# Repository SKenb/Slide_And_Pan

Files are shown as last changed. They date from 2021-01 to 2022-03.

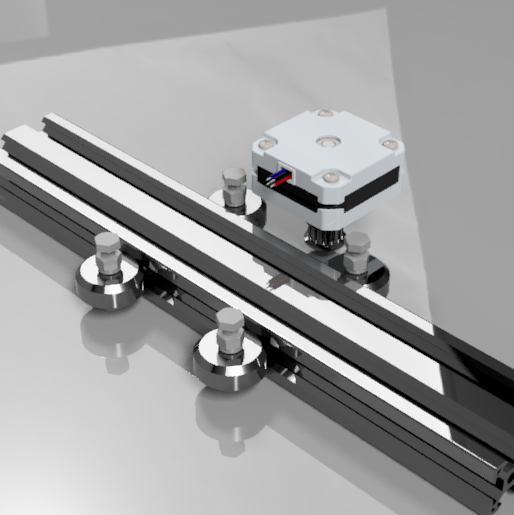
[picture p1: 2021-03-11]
Construction/Images/Slider_2 v50_SlideModule_FrontLeft.png

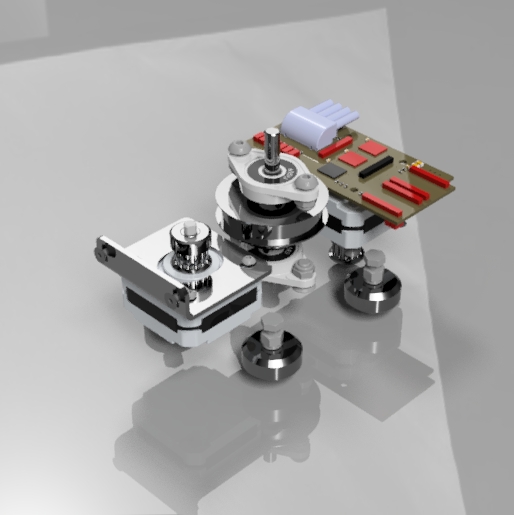
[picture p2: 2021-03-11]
Construction/Images/Slider_2 v50_N_5.png

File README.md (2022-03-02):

# Slide and Pan

## Overview 

    To give a timelapse that special touch, movement is essential. With this simple self-made and inexpensive slider, one can easily achieve that.

"Slide and Pan" stands for a small, compact, and "all in one" DIY slider.

### All in one

_Just place the Slider and start shooting._

The solution provides one small, solid metal box. (55 x 50 x 145 mm - TODO kg). So all required electronics and mechanics in it and no further motors, batteries, control devices are needed.

### Cheap

_Adjust the expenses to your budget._

One key argument for building an own Slider is the relatively small expenses compared to conventional Sliders. One might also think of requesting prepared or finished parts within a fair price ...

### DIY

_You are the boss_

The plans are no secret and easily be replicated by yourself. Just have a look at the public construction plans or come up with your own modified version.

### App

_Easy control_

Use the built-in rotary encoder or the App, to control the Slider. The App makes it very comfortable to set up movements and plan your shots.

## FEATURES

### Slide

Add linear movement to your Timelapse with the Slide-Feature.
Thereby, the Slider moves along a normed Alu-Profile, and thus any length you can think of is possible...

### Pan

Add some gorgeous rotation to your Timelapse
Keep the Milky Way in the center of the frame or focus another lovely spot during your shooting with the feature of (infinity) rotation of your camera ...

### TRACK

Use the Slider as Star-Tracker and realize detailed DeepSky exposures....

### Control

Select one of the predefined shots with the rotary-encoder or set up a detailed exposure/Timelapse with the inbuilt App...

### Compact

One of the most important factors is to have a small, compact and all in one gadget which fits in every backpack...

### Standalone

Everything included and thus no additional material is needed...

### Powerful

2 x 1500 mAh
Two powerful LiPo-batteries provide Slider with enough energy for several hours of shooting....

### Versatile

Nearly every position and movement one might think of is possible ...

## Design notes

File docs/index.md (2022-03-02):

# Slide and Pan

## Overview 

    To give a timelapse that special touch, movement is essential. With this simple self-made and inexpensive slider, one can easily achieve that.

"Slide and Pan" stands for a small, compact, and "all in one" DIY slider.

### All in one

_Just place the Slider and start shooting._

The solution provides one small, solid metal box. (55 x 50 x 145 mm - TODO kg). So all required electronics and mechanics in it and no further motors, batteries, control devices are needed.

### Cheap

_Adjust the expenses to your budget._

One key argument for building an own Slider is the relatively small expenses compared to conventional Sliders. One might also think of requesting prepared or finished parts within a fair price ...

### DIY

_You are the boss_

The plans are no secret and easily be replicated by yourself. Just have a look at the public construction plans or come up with your own modified version.

### App

_Easy control_

Use the built-in rotary encoder or the App, to control the Slider. The App makes it very comfortable to set up movements and plan your shots.

## FEATURES

### Slide

Add linear movement to your Timelapse with the Slide-Feature.
Thereby, the Slider moves along a normed Alu-Profile, and thus any length you can think of is possible...

### Pan

Add some gorgeous rotation to your Timelapse
Keep the Milky Way in the center of the frame or focus another lovely spot during your shooting with the feature of (infinity) rotation of your camera ...

### TRACK

Use the Slider as Star-Tracker and realize detailed DeepSky exposures....

### Control

Select one of the predefined shots with the rotary-encoder or set up a detailed exposure/Timelapse with the inbuilt App...

### Compact

One of the most important factors is to have a small, compact and all in one gadget which fits in every backpack...

### Standalone

Everything included and thus no additional material is needed...

### Powerful

2 x 1500 mAh
Two powerful LiPo-batteries provide Slider with enough energy for several hours of shooting....

### Versatile

Nearly every position and movement one might think of is possible ...

## Welcome to GitHub Pages

You can use the [editor on GitHub](https://github.com/SKenb/Slide_And_Pan/edit/master/docs/index.md) to maintain and preview the content for your website in Markdown files.

Whenever you commit to this repository, GitHub Pages will run [Jekyll](https://jekyllrb.com/) to rebuild the pages in your site, from the content in your Markdown files.

### Markdown

Markdown is a lightweight and easy-to-use syntax for styling your writing. It includes conventions for

```markdown
Syntax highlighted code block

# Header 1
## Header 2
### Header 3

- Bulleted
- List

1. Numbered
2. List

**Bold** and _Italic_ and `Code` text

[Link](url) and ![Image](src)
```

For more details see [Basic writing and formatting syntax](https://docs.github.com/en/github/writing-on-github/getting-started-with-writing-and-formatting-on-github/basic-writing-and-formatting-syntax).

### Jekyll Themes

Your Pages site will use the layout and styles from the Jekyll theme you have selected in your [repository settings](https://github.com/SKenb/Slide_And_Pan/settings/pages). The name of this theme is saved in the Jekyll `_config.yml` configuration file.

### Support or Contact

Having trouble with Pages? Check out our [documentation](https://docs.github.com/categories/github-pages-basics/) or [contact support](https://support.github.com/contact) and we’ll help you sort it out.

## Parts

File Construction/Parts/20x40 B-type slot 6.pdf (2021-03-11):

# Profile 20x40 B-Type slot 6

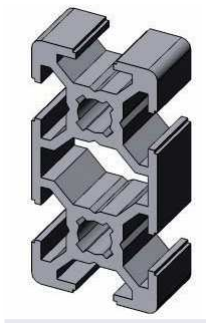
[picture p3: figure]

Profile 20x40 B-Type slot 6

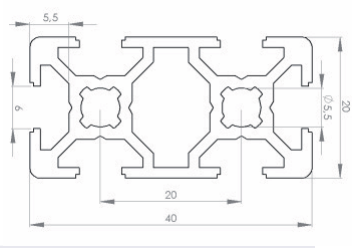
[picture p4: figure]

Slot | | 6 | mm
Mass | m | 0,80 | Kg/m
Moment of Inertia | Ix | 4,60 | cm⁴
| Iy | 1,20 | cm⁴
Section modulus | Wx | 2,50 | cm³
| Wy | 1,40 | cm³
Surface | A | 2,90 | cm²

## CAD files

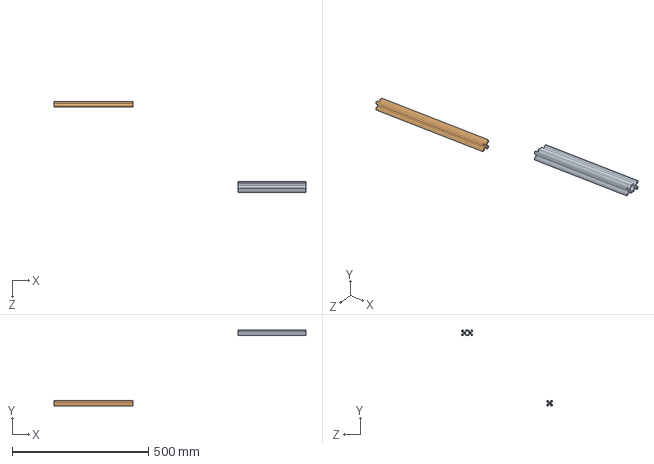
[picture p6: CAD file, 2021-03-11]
Construction/Parts/v-slot-profiles-20x20-20x40-1.snapshot.5/V - slot profiles (20x20 & 20x40).SLDASM
923.9 x 277.7 x 331.8 mm
v-20x40 alluminum profile
V-2020 alluminum profile

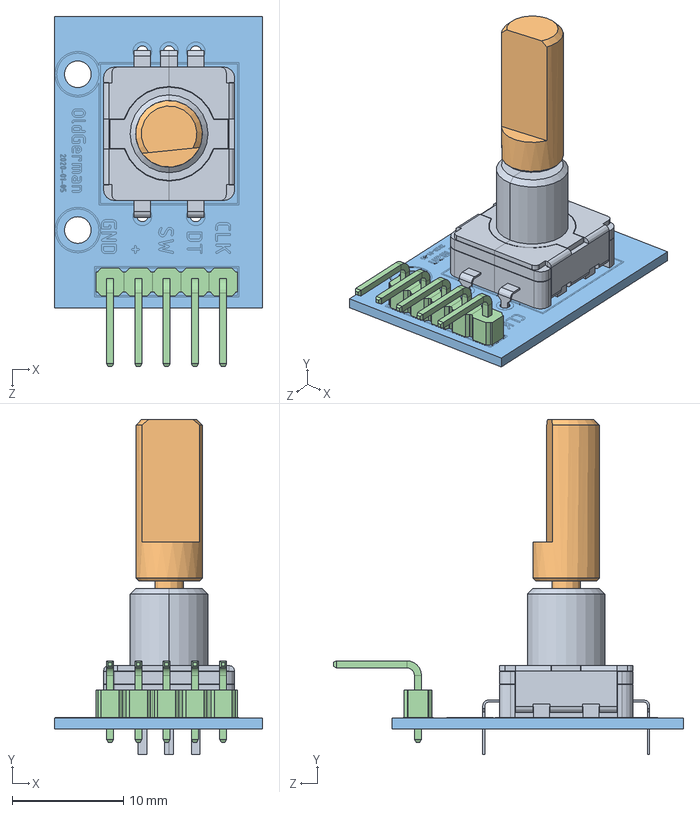
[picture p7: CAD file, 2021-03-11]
Construction/Parts/ky-040-rotary-encoder-1.snapshot.1/Rotary Encoder - ODG/sw2017 model/KY-040 Rotary Encoder.SLDASM
18.7 x 30.1 x 31.5 mm
Rotary Encoder
D-handle
pcb
2.54 5PIN 90

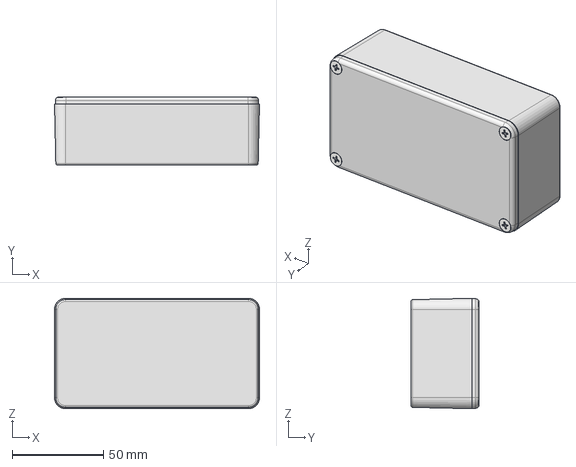
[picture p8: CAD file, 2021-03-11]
Construction/Parts/1590B2/1590B2.stp
112.4 x 37.5 x 60.5 mm
1590B2 BOX
1590B-BS LID

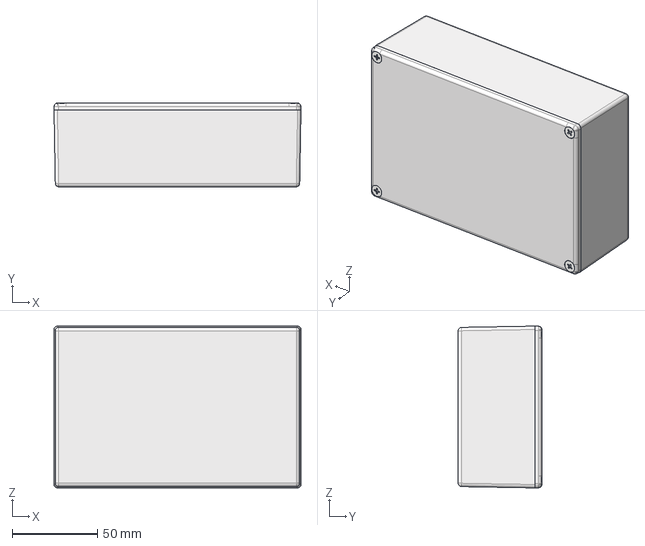
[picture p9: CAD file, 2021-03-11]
Construction/Parts/1590J/1590J.stp
145.0 x 49.1 x 95.0 mm

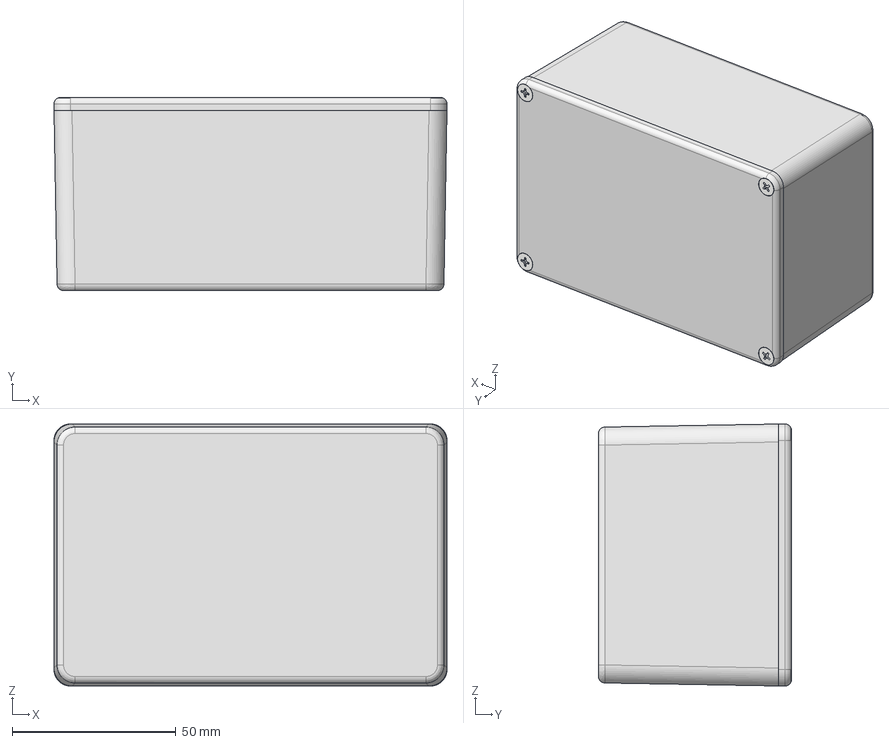
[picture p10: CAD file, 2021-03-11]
Construction/Parts/1590T/1590T.stp
120.0 x 59.0 x 80.0 mm

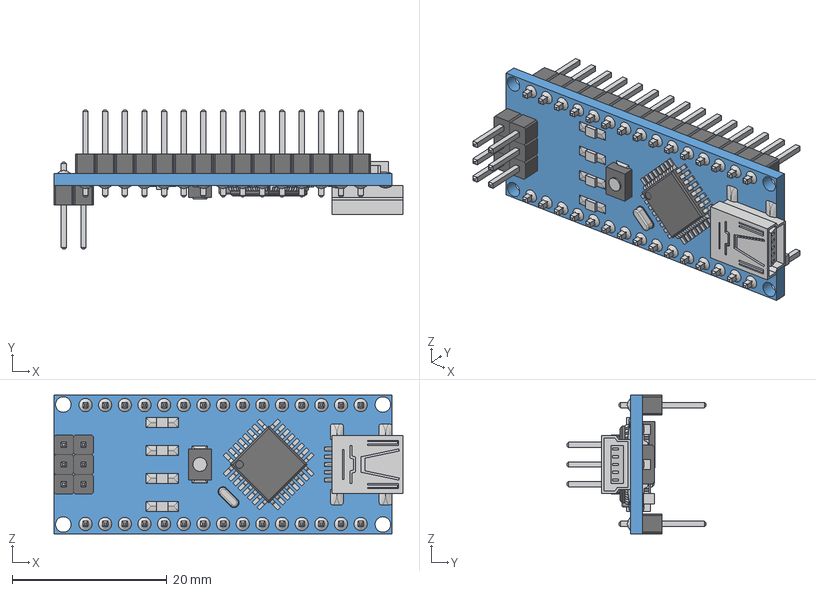
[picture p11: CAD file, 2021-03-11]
Construction/Parts/arduino-nano-v3-2.snapshot.6/Arduino Nano V3.step
45.1 x 18.0 x 17.9 mm
switch
Led x 3
Led (1)
Pin x 21
chip1
USB
Crystal
Pin (1) x 15
Res x 5
cap x 2
Chip
respack x 2
diode
vreg

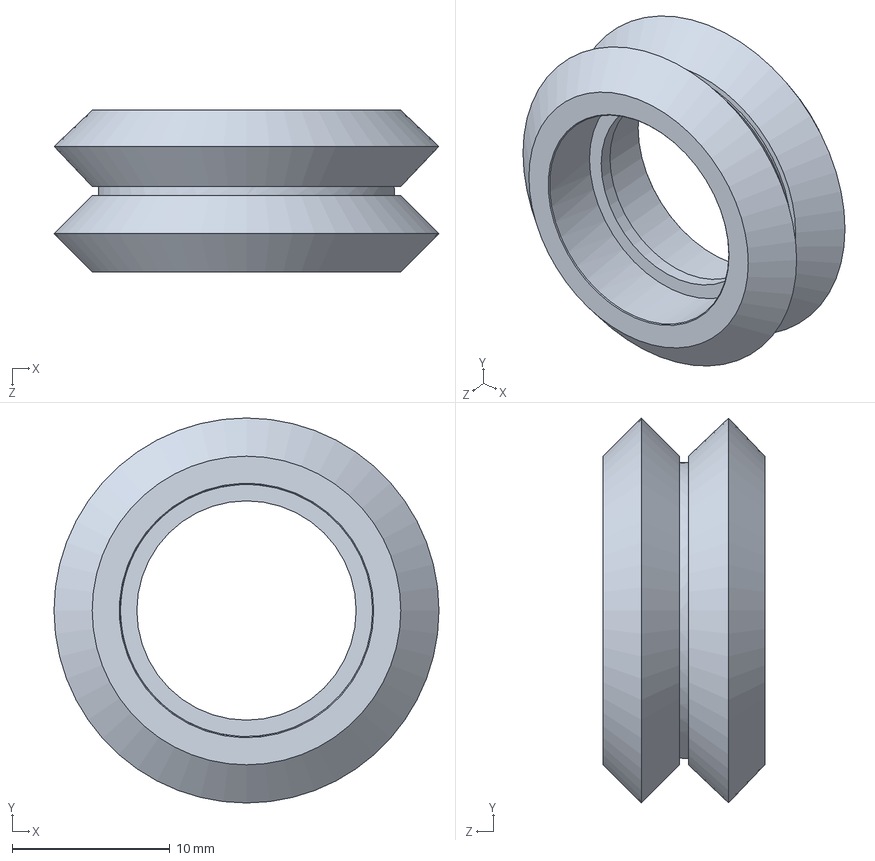
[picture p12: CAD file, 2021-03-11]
Construction/Parts/d-24mm-v-slot-wheel-bearings-motion-1.snapshot.4/V-slot wheel.SLDPRT
24.4 x 24.4 x 10.2 mm

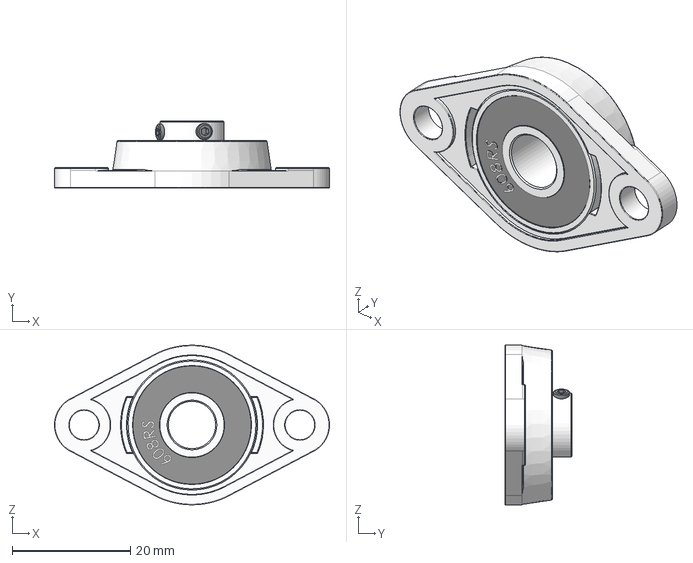
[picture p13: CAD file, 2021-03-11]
Construction/Parts/kfl08-mancal-flange-oval-o8-1.snapshot.1/KFL08 - Mancal Flange oval Ø8.stp
46.5 x 11.4 x 27.0 mm

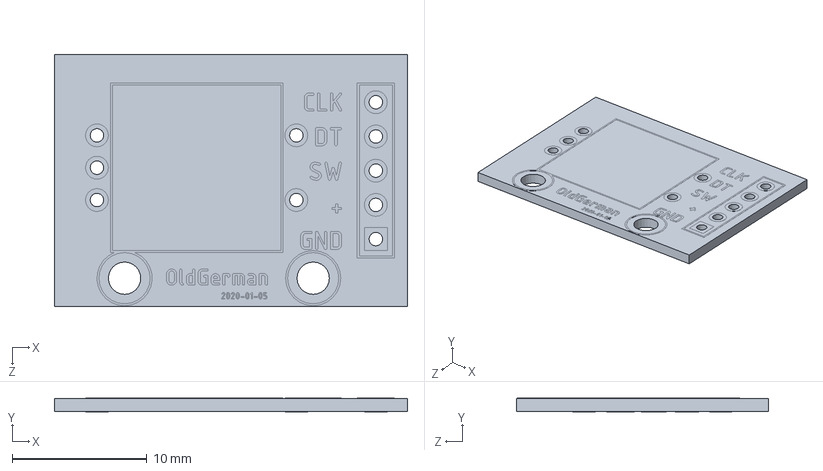
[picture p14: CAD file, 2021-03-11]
Construction/Parts/ky-040-rotary-encoder-1.snapshot.1/Rotary Encoder - ODG/sw2017 model/pcb.SLDPRT
26.2 x 1.02 x 18.7 mm

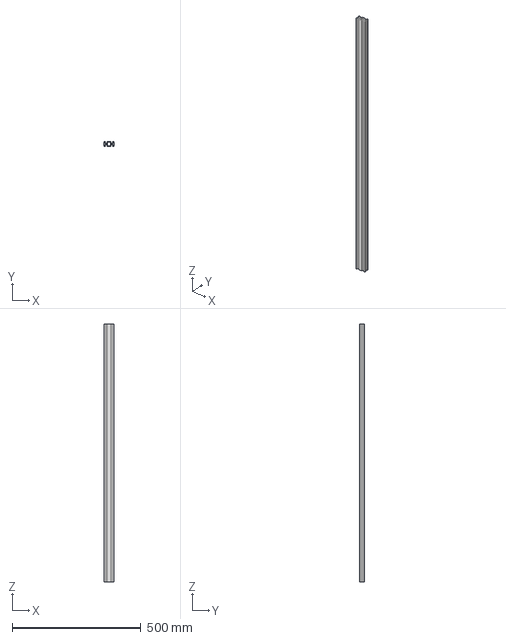
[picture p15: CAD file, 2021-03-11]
Construction/Parts/Motedis Profile 20x40 B-Type slot 6/Motedis Profile 20x40 B-Type slot 6.stp
40.0 x 20.0 x 1000.0 mm

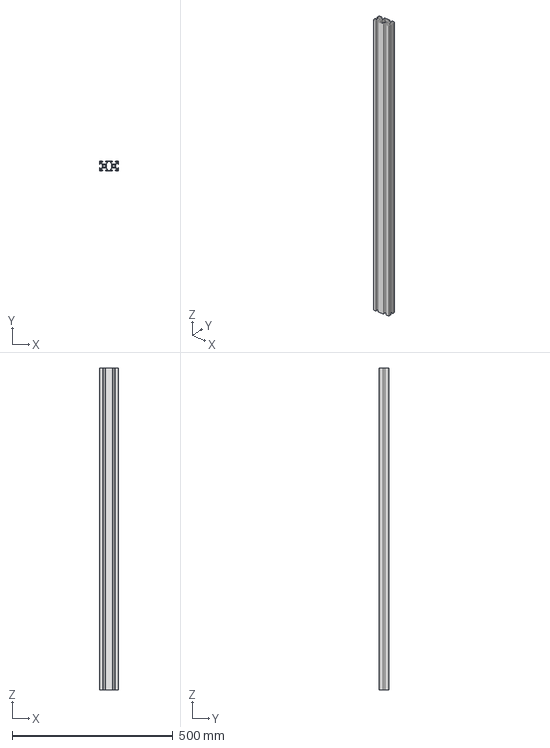
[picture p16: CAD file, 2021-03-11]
Construction/Parts/Motedis Profile 30x60 B-Type slot 8/Motedis Profile 30x60 B-Type slot 8.stp
60.0 x 30.0 x 1000.0 mm

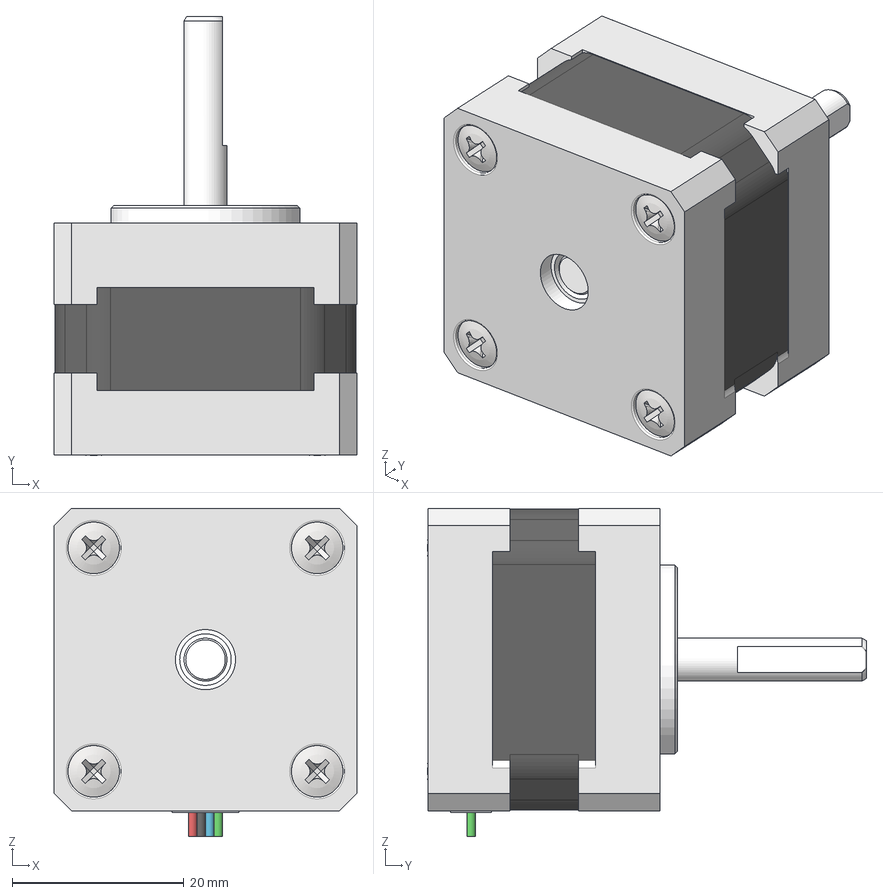
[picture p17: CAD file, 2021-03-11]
Construction/Parts/nema-14-stepper-motor-6.snapshot.2/NEMA_14HM11-0404S.stp
35.2 x 51.1 x 38.2 mm
NEMA_14HM11-0404S_1
NEMA_14HM11-0404S_SHAFT
JIS B 1111 (H) - M3x6 - 4.8 x 4

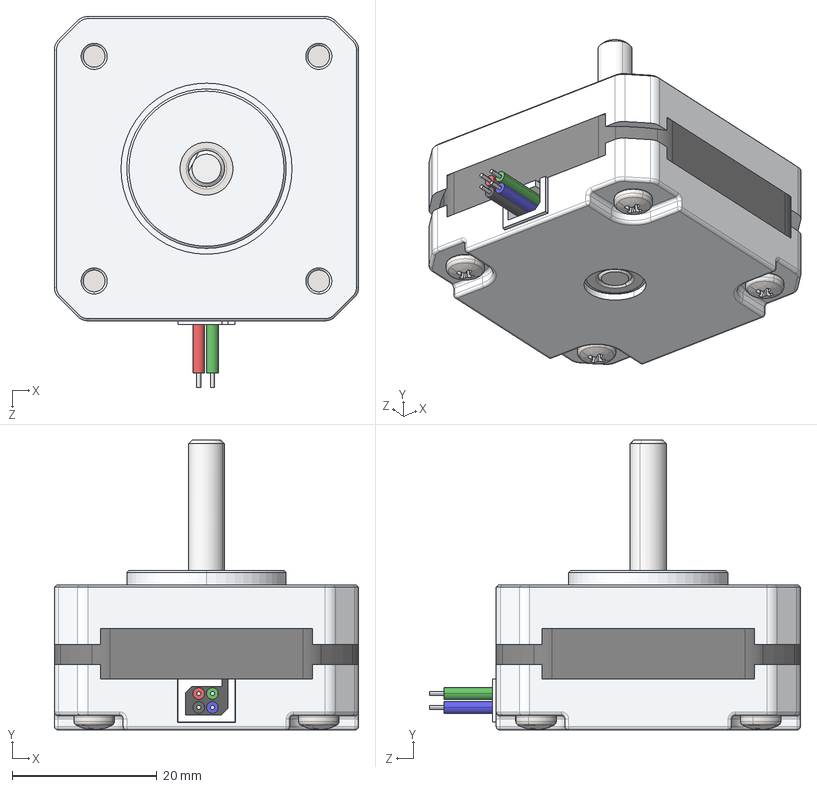
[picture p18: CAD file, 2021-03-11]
Construction/Parts/nema-17-20mm-stepper-motor-1.snapshot.10/17HS08-1004S/17HS08-1004S.STEP
42.0 x 40.0 x 51.2 mm

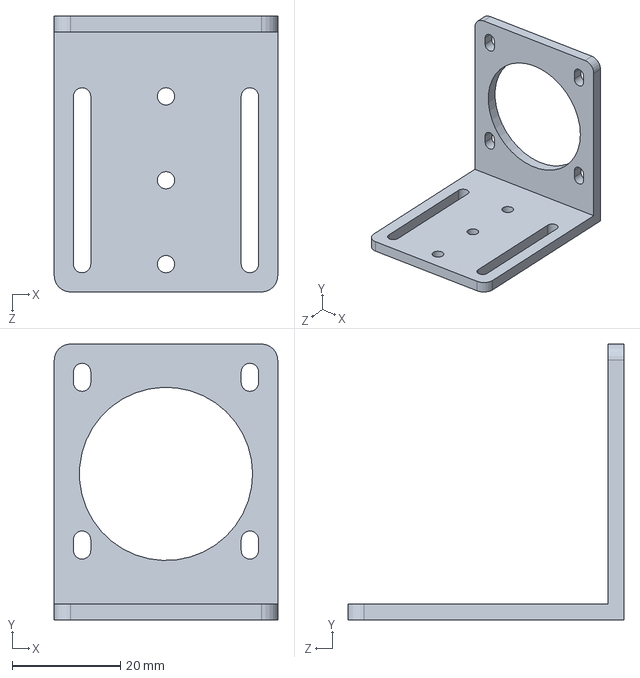
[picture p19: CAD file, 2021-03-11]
Construction/Parts/nema-17-bracket-2.snapshot.1/nema bracket.SLDPRT
41.3 x 51.0 x 51.0 mm

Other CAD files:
Construction/Parts/nema-17-l-bracket-1.snapshot.1/Nema17 Lbeugel.SLDPRT
Construction/Parts/pololu-stamped-aluminum-l-bracket-for-nema-14-stepper-motors-1.snapshot.2/LBracket.igs
Construction/Parts/pulley.SLDPRT
Construction/Parts/Schrauben/KIPP_K0708305X10/K0708.305X10.stl
Construction/Parts/1590B2/1590B2.igs
Construction/Parts/1590J/1590J.igs
Construction/Parts/1590T/1590T.igs
Construction/Parts/arduino-nano-v3-2.snapshot.6/Arduino NanoV3 + Female Headers.step
Construction/Parts/d-24mm-v-slot-wheel-bearings-motion-1.snapshot.4/instrument ball bearing_68_am.sldprt
Construction/Parts/kfl08-mancal-flange-oval-o8-1.snapshot.1/KFL08 - Mancal Flange oval Ø8.ipt
Construction/Parts/ky-040-rotary-encoder-1.snapshot.1/Rotary Encoder - ODG/sw2017 model/2.54 5PIN 90.SLDPRT
Construction/Parts/ky-040-rotary-encoder-1.snapshot.1/Rotary Encoder - ODG/sw2017 model/D-handle.SLDPRT
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

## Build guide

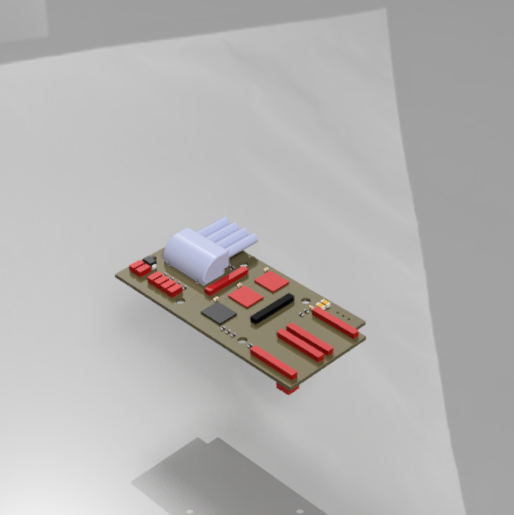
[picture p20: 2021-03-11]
Construction/Images/Slider_2 v50_Etech_side.png

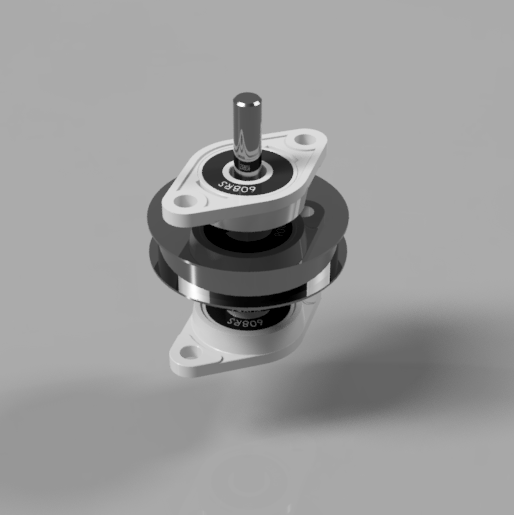
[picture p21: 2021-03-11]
Construction/Images/Slider_2 v50_Pan_Axis_Lager.png

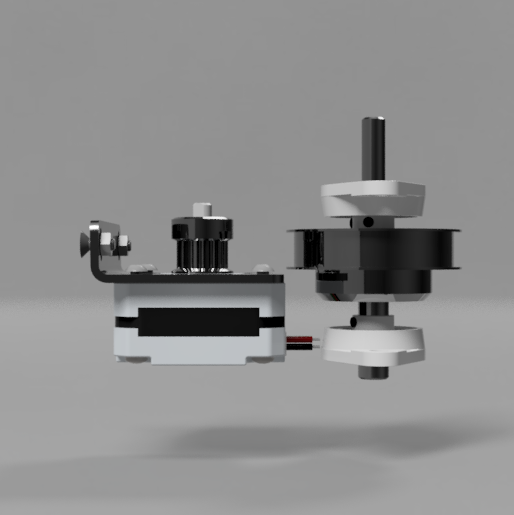
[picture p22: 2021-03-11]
Construction/Images/Slider_2 v50_PAn_Module_Side_2.png

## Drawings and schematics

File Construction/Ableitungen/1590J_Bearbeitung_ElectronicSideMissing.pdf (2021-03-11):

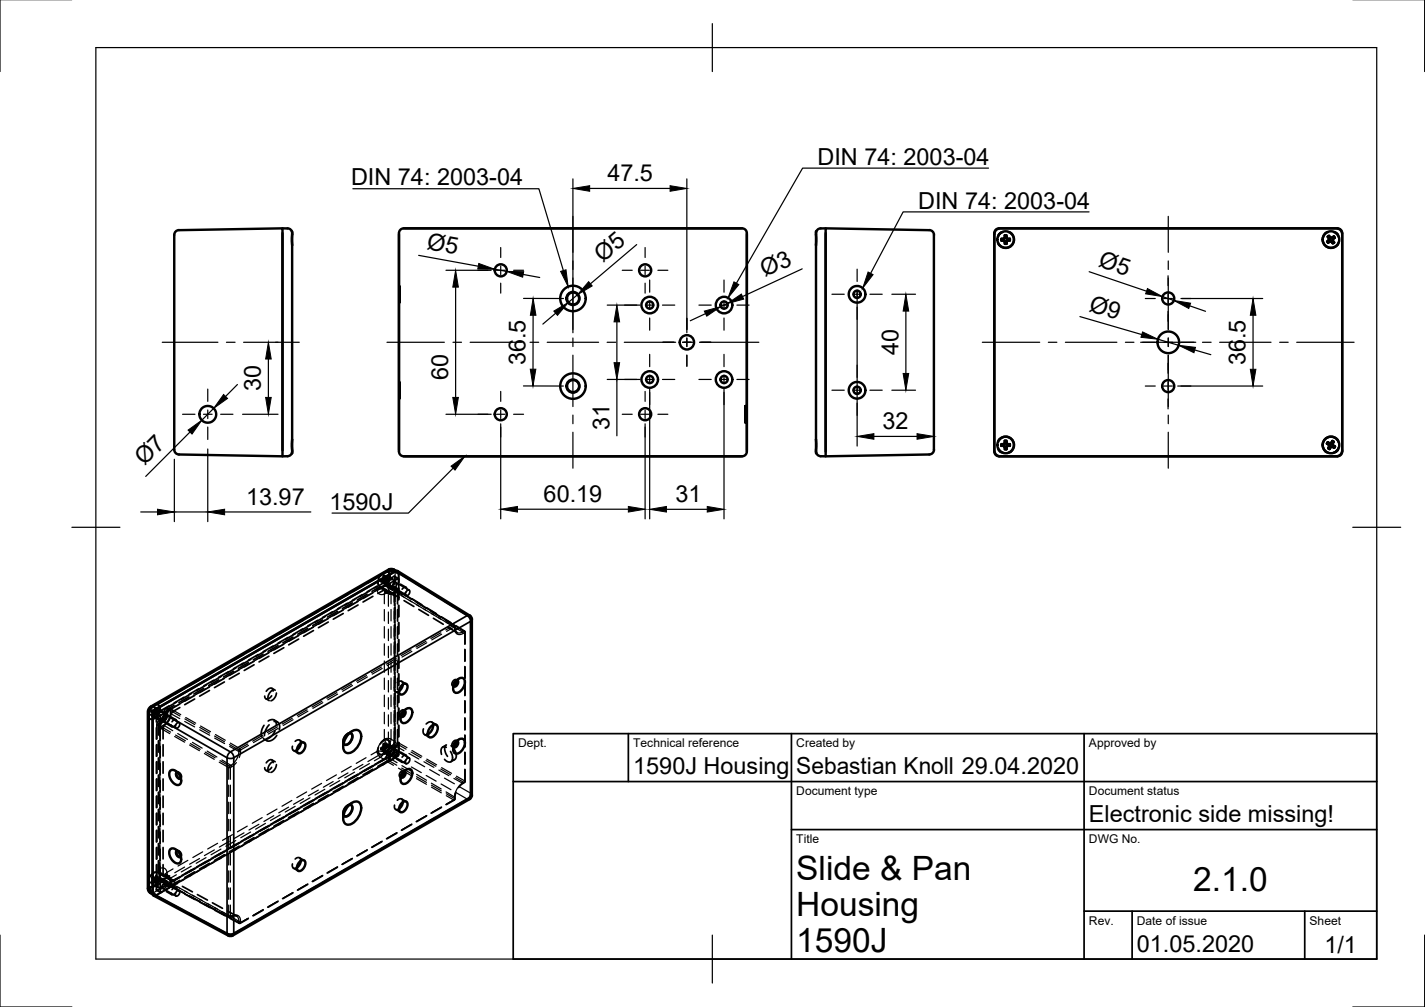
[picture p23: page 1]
DIN 74: 2003-04; DIN 74: 2003-04 40; DIN 74: 2003-04 30

Dept. | Technical reference 1590J Housing | Created by Sebastian Knoll 29.04.2020 | Approved by

Document type | Document status Electronic side missing!

Title Housing 1590J | DWG No. 2.1.0 Slide & Pan

Rev. | Date of issue 01.05.2020 | Sheet 1/1

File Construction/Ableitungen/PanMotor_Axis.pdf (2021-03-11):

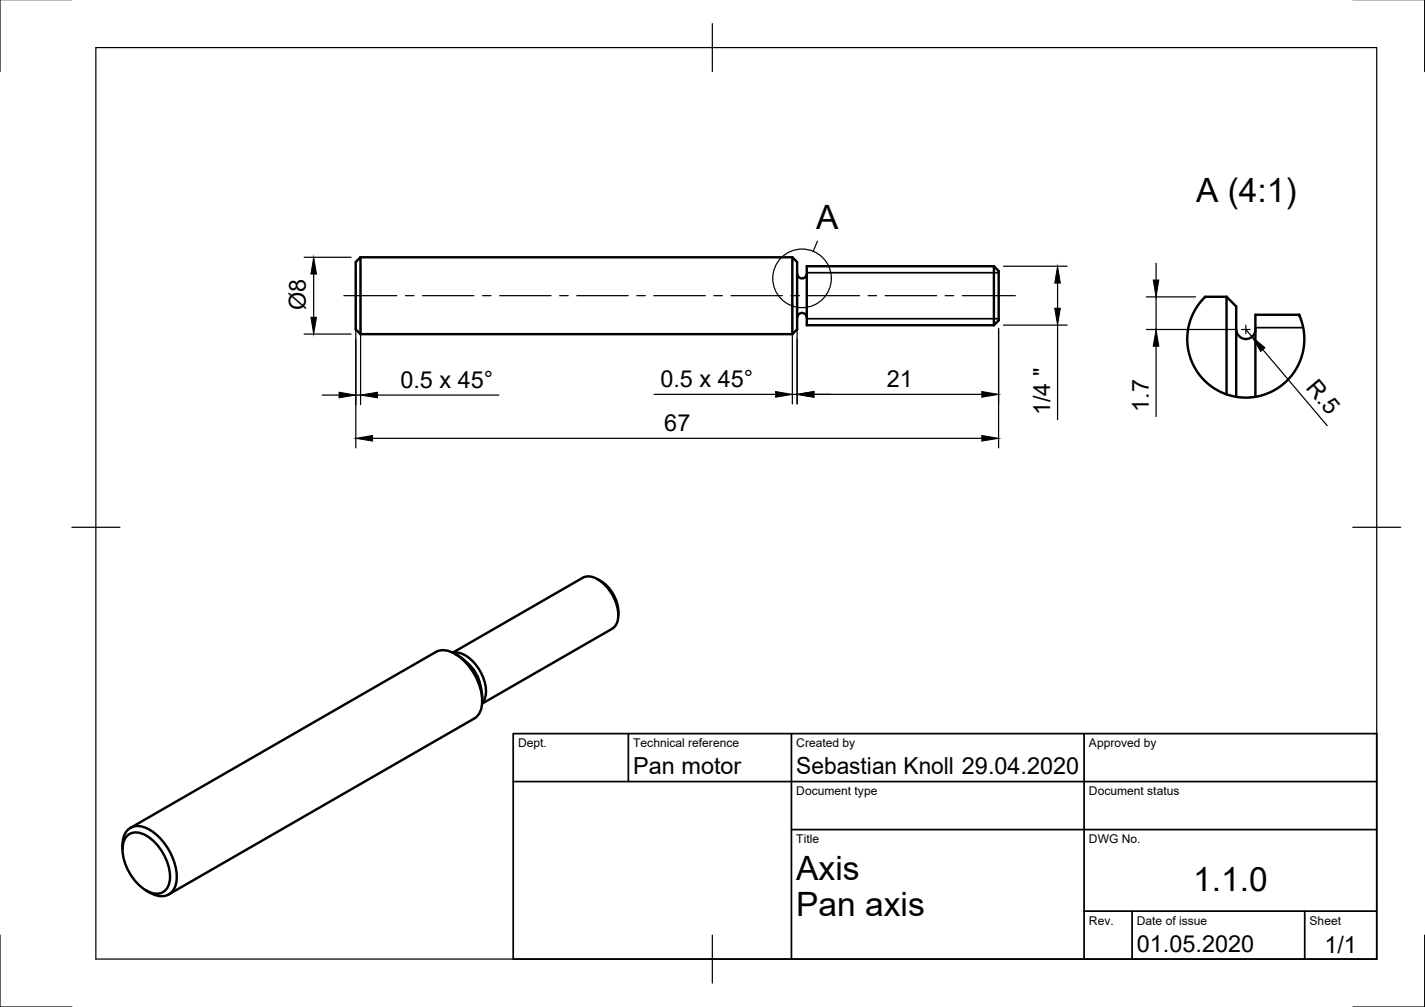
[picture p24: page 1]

Dept. | Technical reference Pan motor | Created by Sebastian Knoll 29.04.2020 | Approved by

Document type | Document status

Title Pan axis | DWG No. 1.1.0 Axis

Rev. | Date of issue 01.05.2020 | Sheet 1/1

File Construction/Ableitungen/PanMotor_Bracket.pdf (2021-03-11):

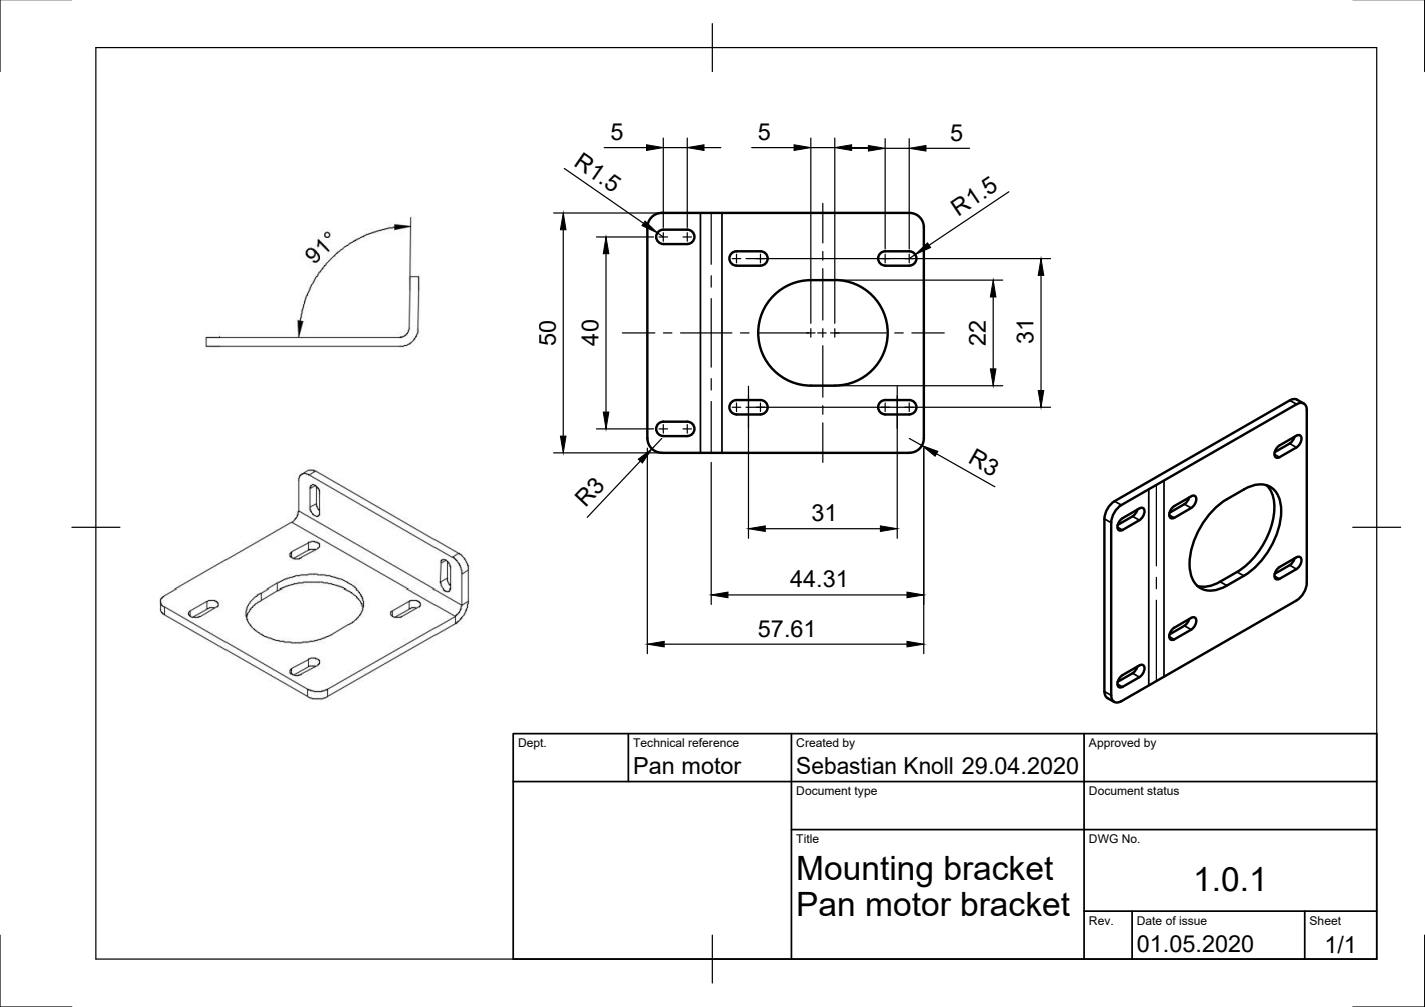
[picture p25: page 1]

Dept. | Technical reference Pan motor | Created by Sebastian Knoll 29.04.2020 | Approved by

Document type | Document status

Title Mounting bracket Pan motor bracket | DWG No. 1.0.1

Rev. | Date of issue 01.05.2020 | Sheet 1/1

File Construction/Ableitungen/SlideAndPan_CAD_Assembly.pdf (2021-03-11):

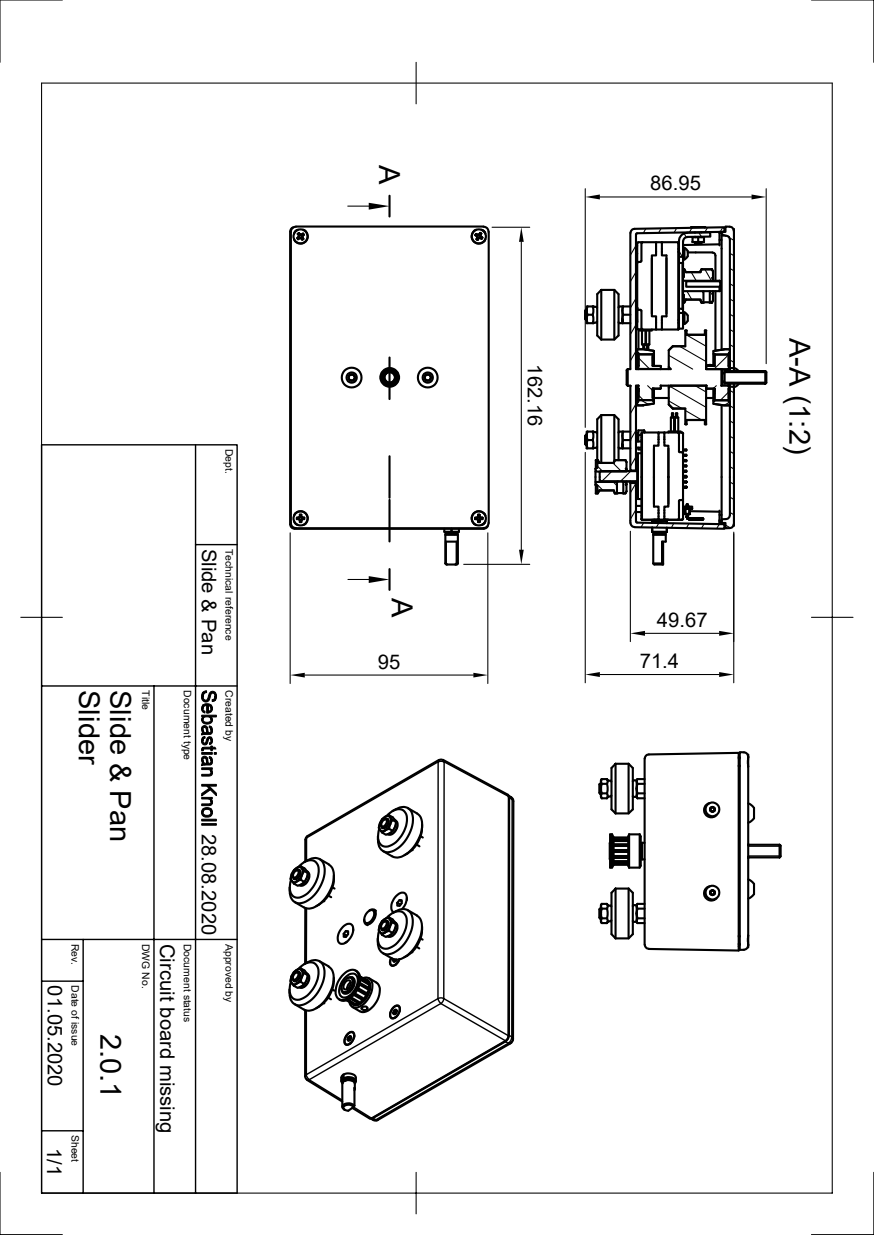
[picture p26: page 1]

Dept. Technical reference Created by Approved by Title DWG No. Document type Document status Rev. Date of issue Sheet 01.05.2020 Circuit board missing 28.08.2020 1/1 Slider 2.0.1 Slide & Pan Slide & Pan

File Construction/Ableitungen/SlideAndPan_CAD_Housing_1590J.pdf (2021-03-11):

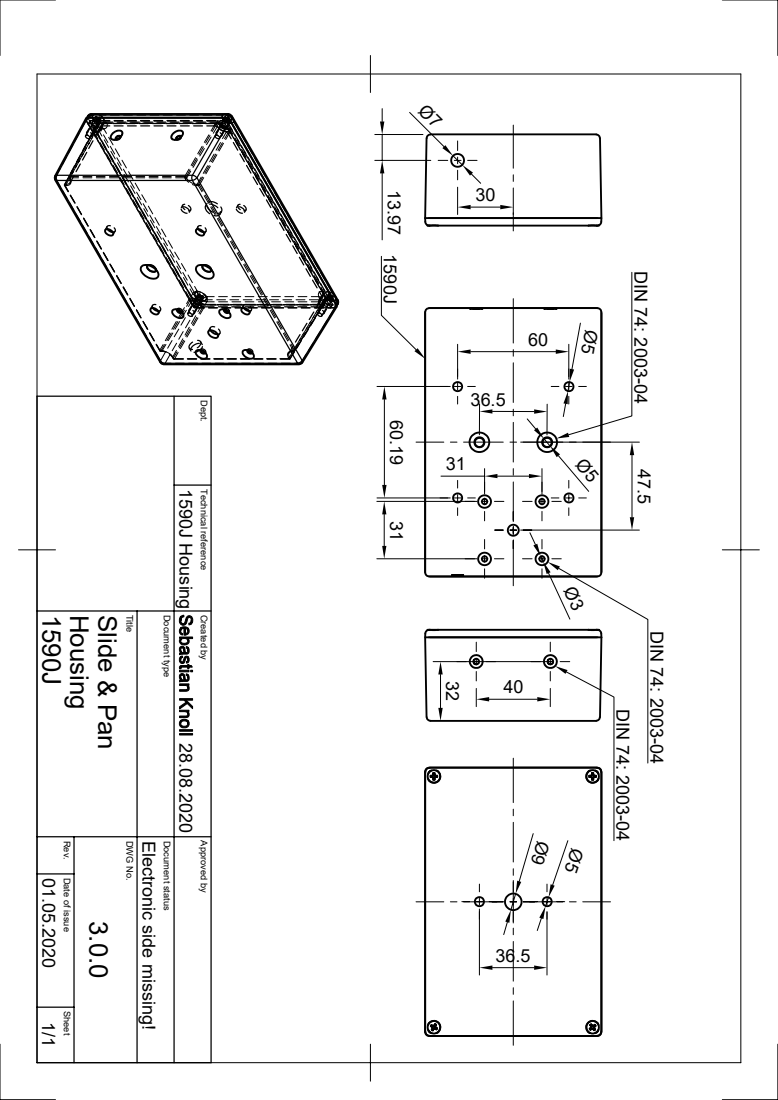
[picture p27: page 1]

Dept. Technical reference Created by Approved by Title DWG No. Document type Document status Rev. Date of issue Sheet 01.05.2020 1590J Electronic side missing! 28.08.2020 1/1 Housing 3.0.0 Slide & Pan 1590J Housing 1590J

Ø3 DIN 74: 2003-04 DIN 74: 2003-04 40 32 DIN 74: 2003-04

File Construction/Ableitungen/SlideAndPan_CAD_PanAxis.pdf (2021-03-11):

# Ø8 0.5 x 45° 0.5 x 45°

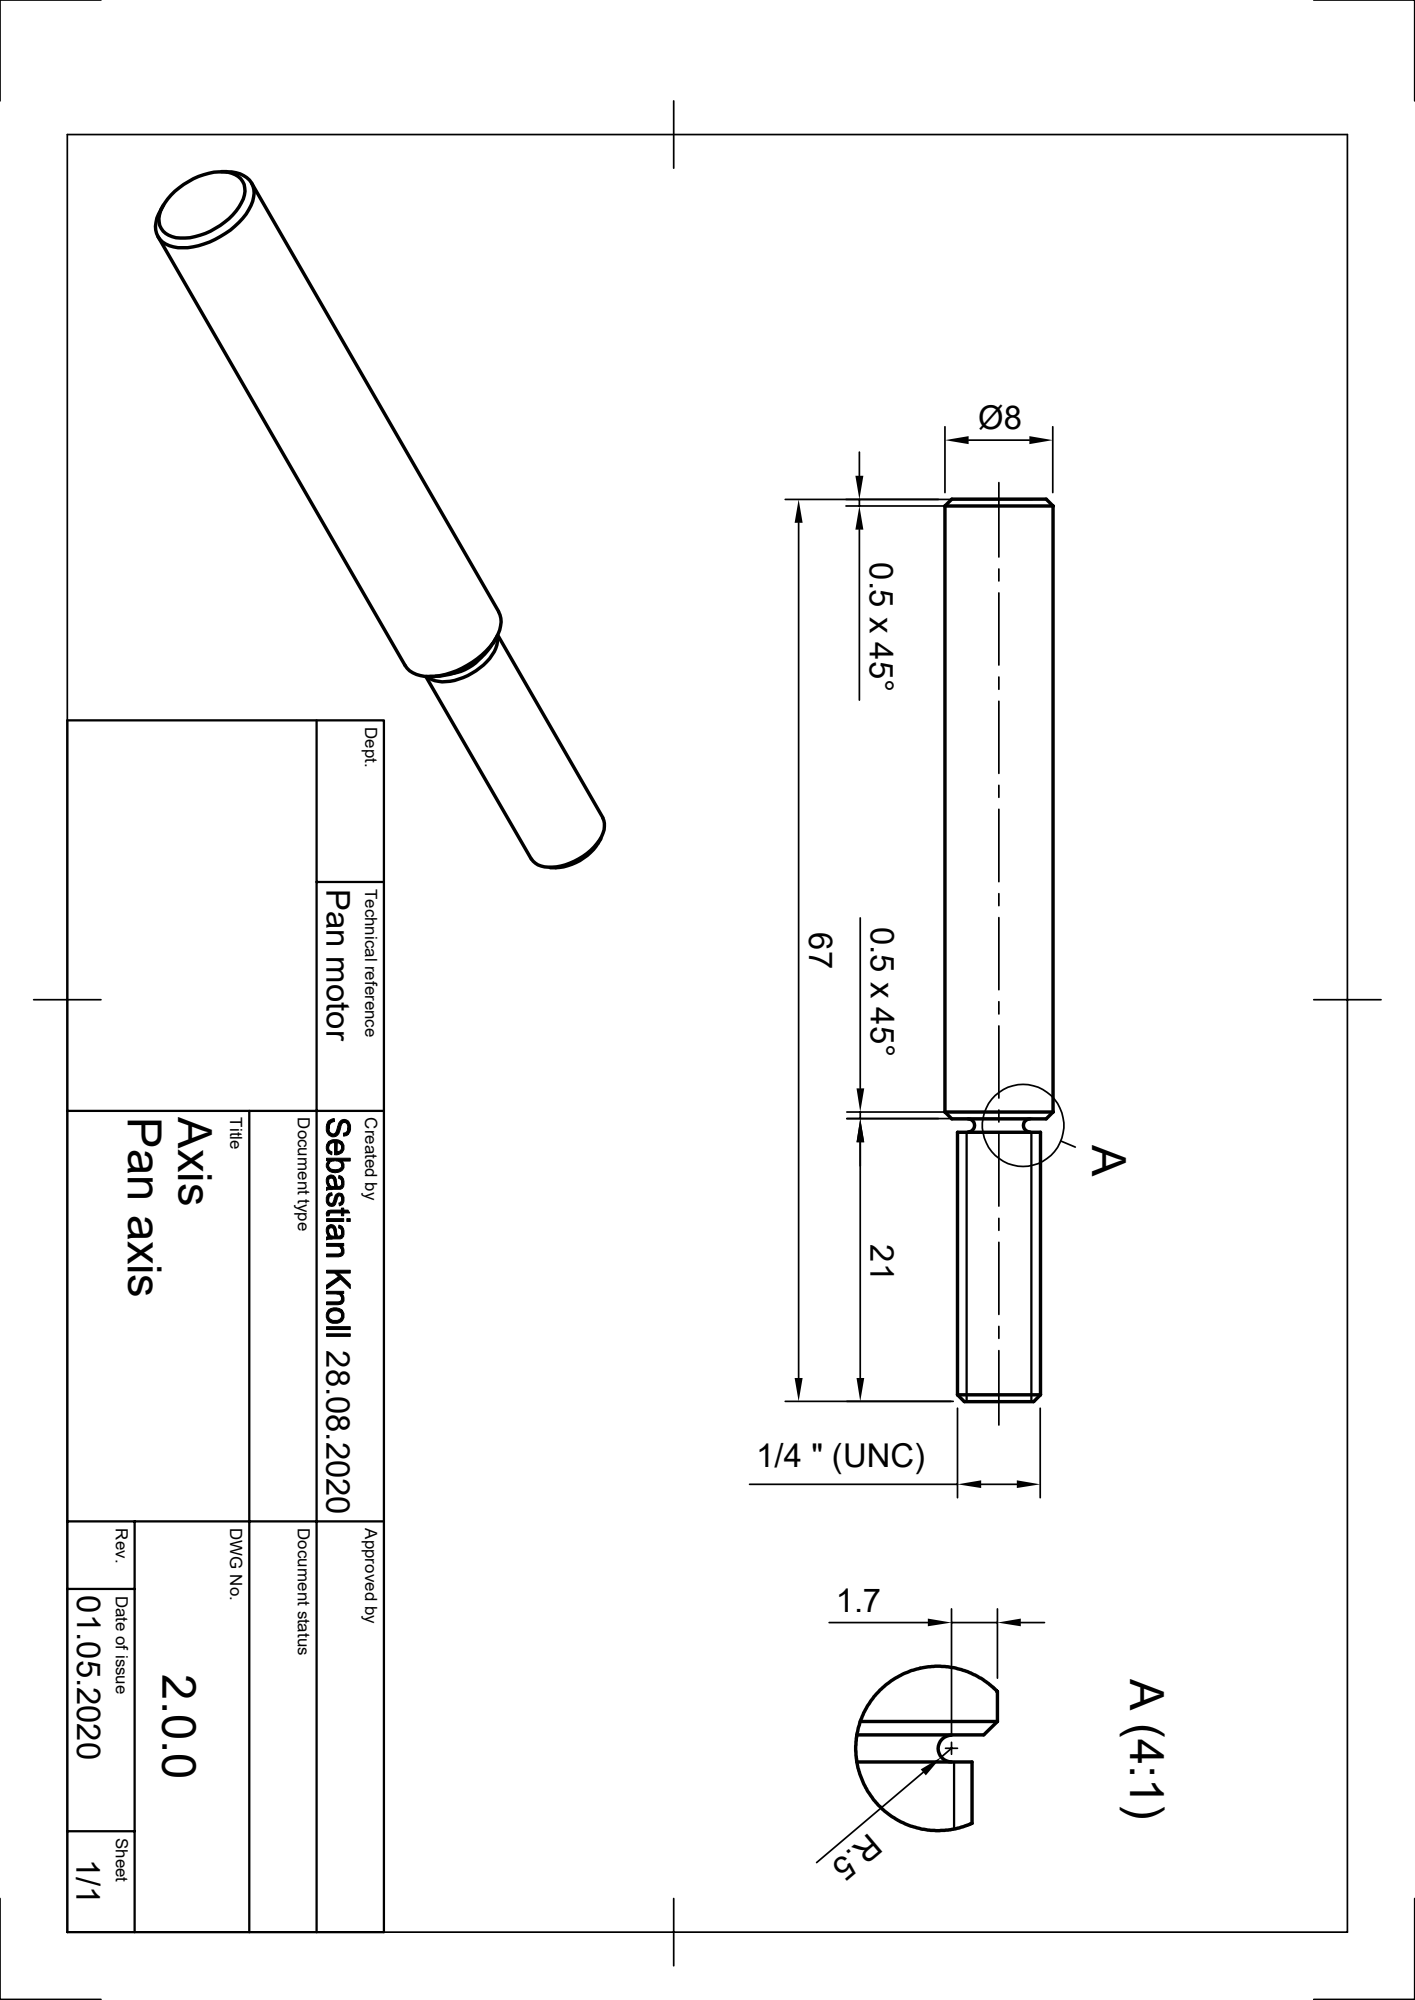
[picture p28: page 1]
1/4 " (UNC) ²¹

Dept. Technical reference Created by Approved by Title DWG No. Document type Document status Rev. Date of issue Sheet 01.05.2020 28.08.2020 1/1 Pan axis 2.0.0 Axis Pan motor 67

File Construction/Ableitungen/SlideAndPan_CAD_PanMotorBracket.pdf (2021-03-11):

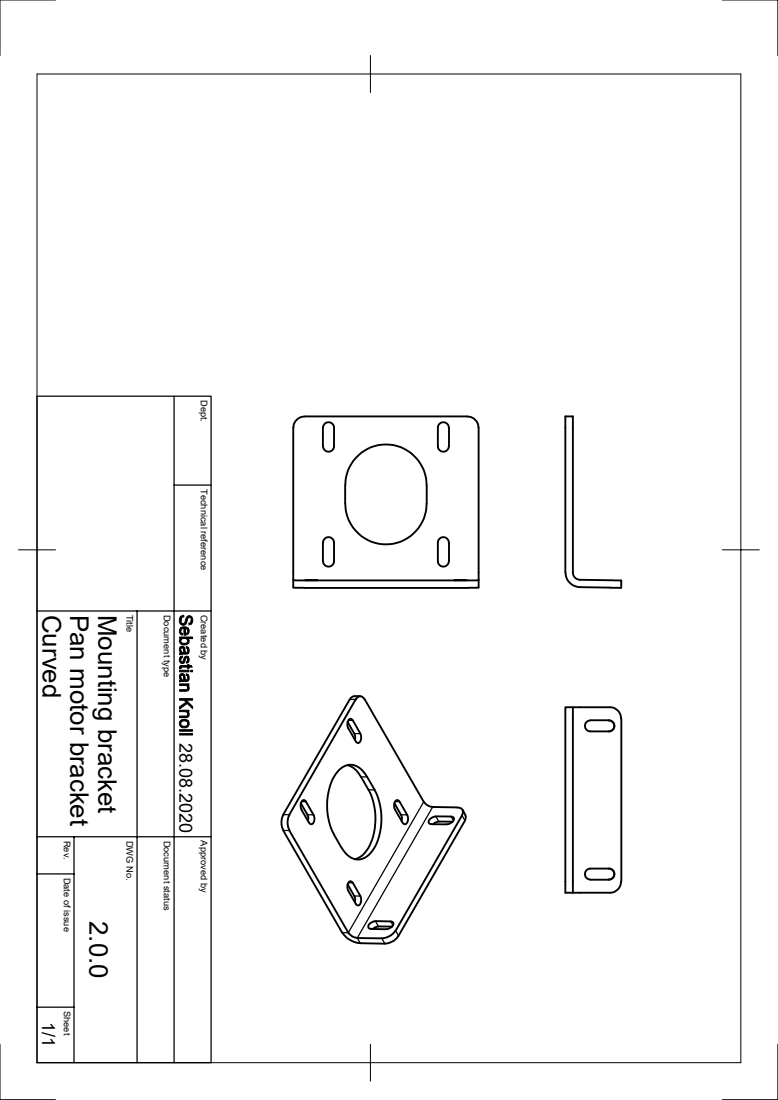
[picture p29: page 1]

Dept. Technical reference Created by Approved by Title DWG No. Document type Document status Rev. Date of issue Sheet Curved 28.08.2020 1/1 Pan motor bracket 2.0.0 Mounting bracket

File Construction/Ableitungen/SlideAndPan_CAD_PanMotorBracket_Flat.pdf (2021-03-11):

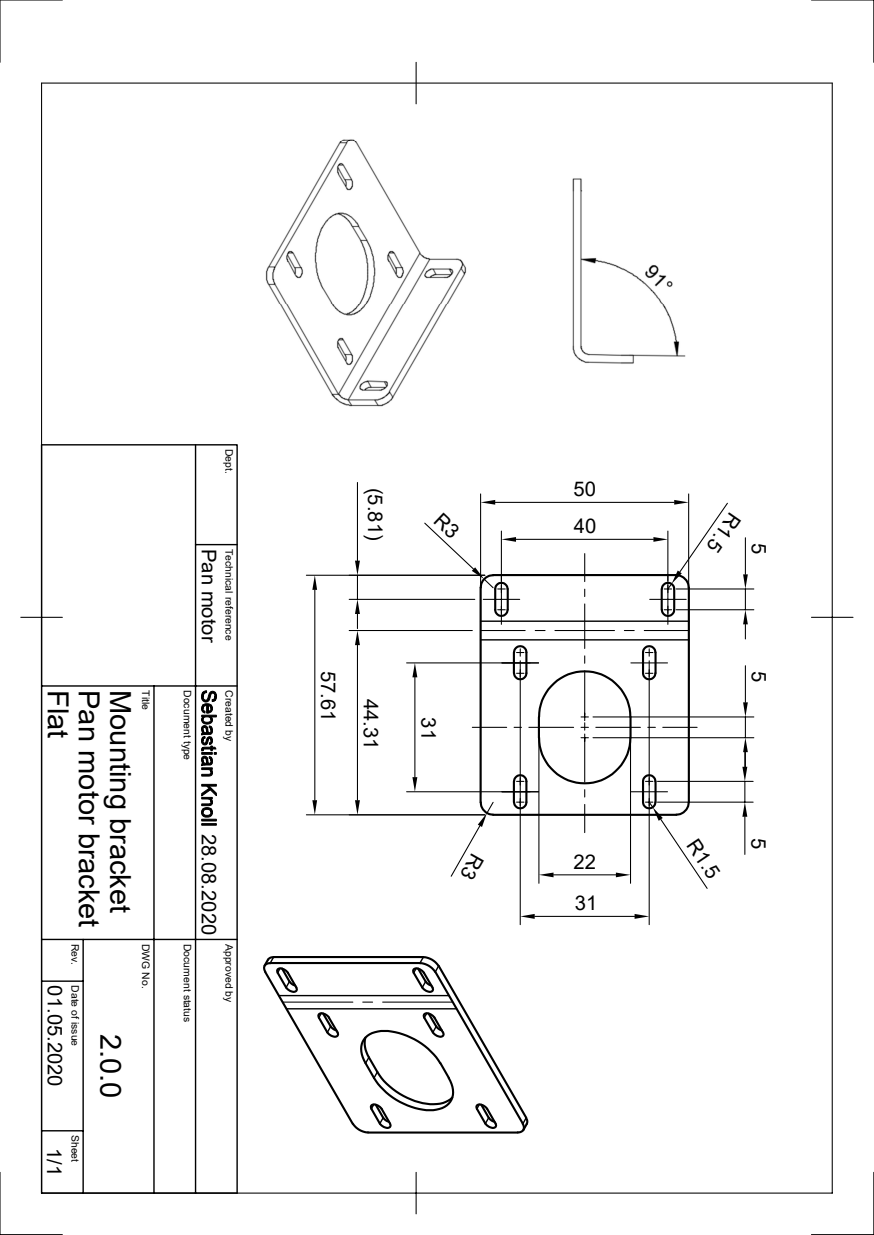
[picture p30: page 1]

Dept. Technical reference Created by Approved by Title DWG No. Document type Document status Rev. Date of issue Sheet 01.05.2020 Flat 28.08.2020 1/1 Pan motor bracket 2.0.0 Mounting bracket Pan motor 57.61

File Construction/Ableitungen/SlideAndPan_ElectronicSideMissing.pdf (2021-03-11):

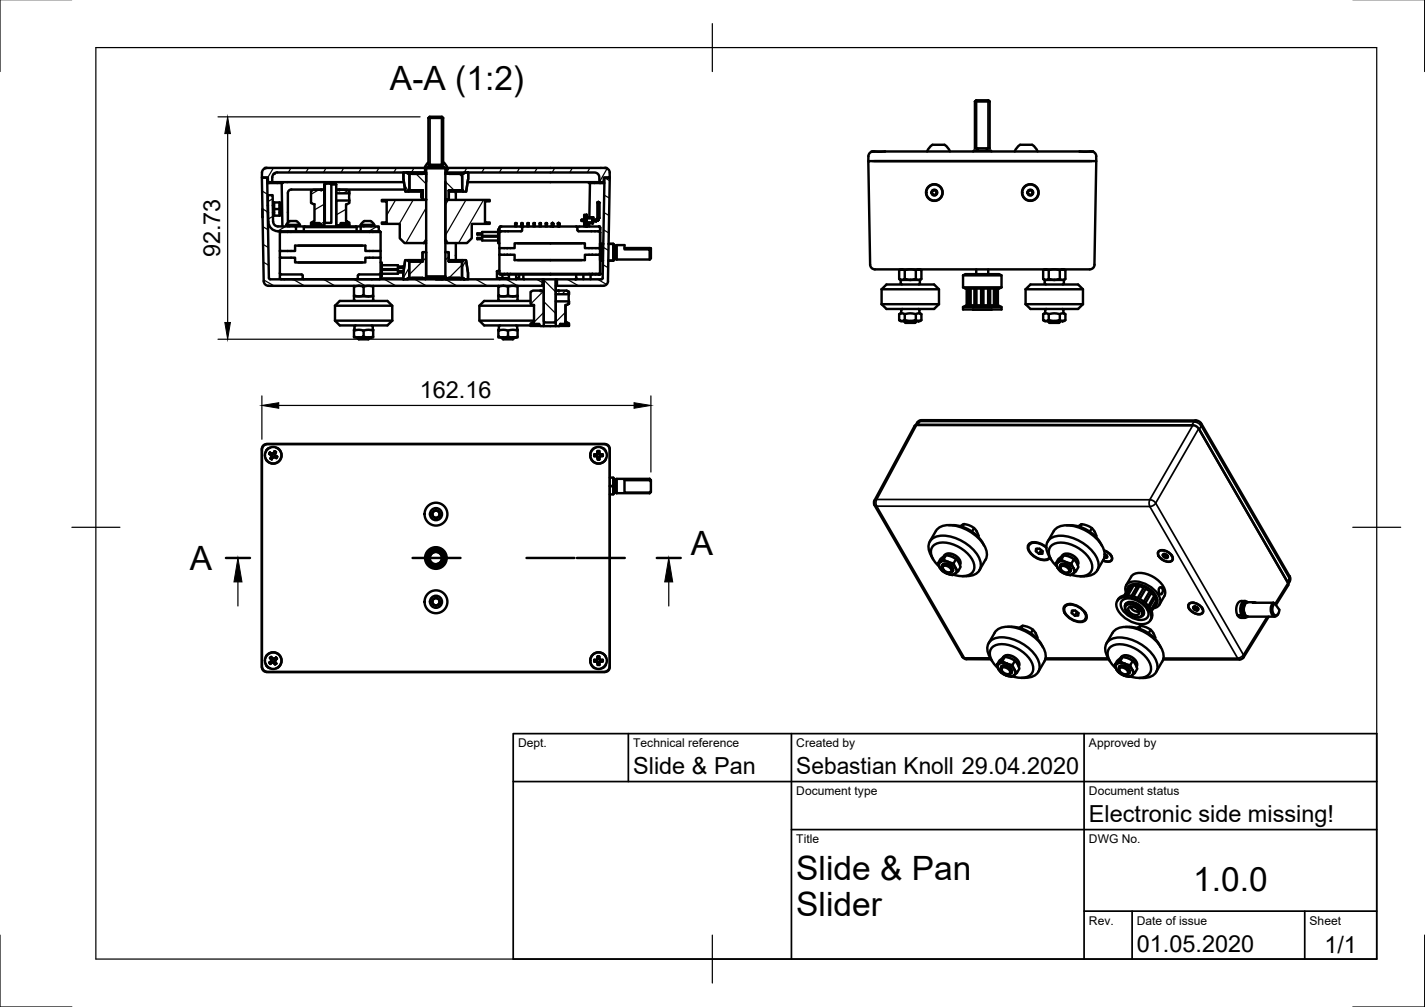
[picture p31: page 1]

Dept. | Technical reference Slide & Pan | Created by Sebastian Knoll 29.04.2020 | Approved by

Document type | Document status Electronic side missing!

Title Slider | DWG No. 1.0.0 Slide & Pan

Rev. | Date of issue 01.05.2020 | Sheet 1/1

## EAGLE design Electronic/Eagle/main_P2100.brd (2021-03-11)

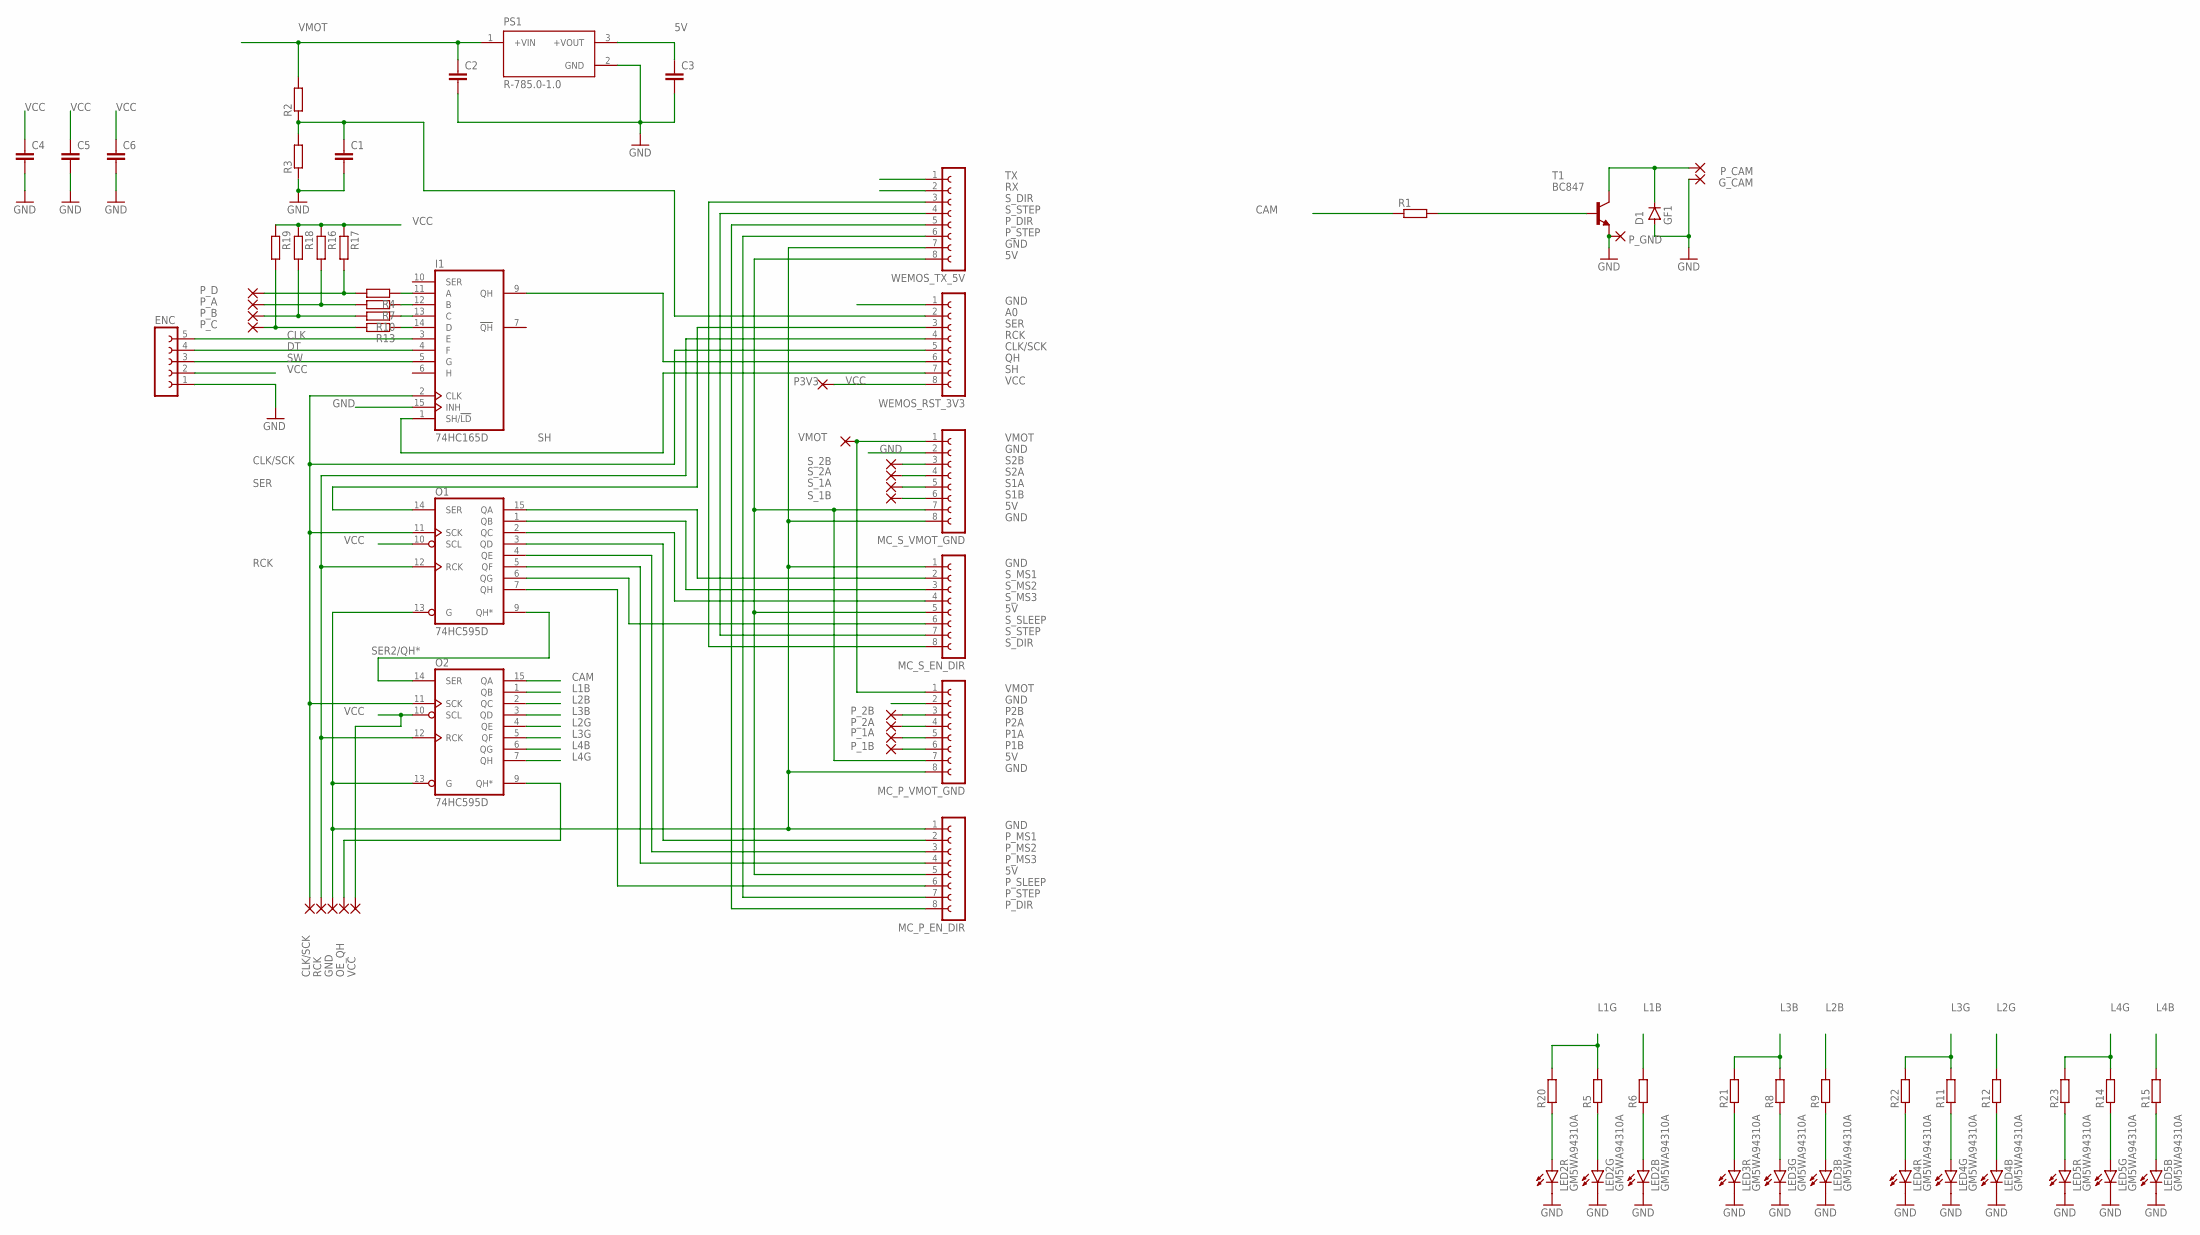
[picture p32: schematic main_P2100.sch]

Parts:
C1, C4, C5, C6: C-EUC0603; C0603
C2, C3: C-EUC1206; C1206
D1: GF1; SMA-DO214AC
ENC: FE05-1
G_CAM: SMD5; SMD2,54-5,08
I1: 74HC165D; SO16
LED2, LED3, LED4, LED5: GM5WA94310A
MC_P_EN_DIR: FE08-1; FE08
MC_P_VMOT_GND: FE08-1; FE08
MC_S_EN_DIR: FE08-1; FE08
MC_S_VMOT_GND: FE08-1; FE08
O1, O2: 74HC595D; SO16
P3V3: SMD5; SMD2,54-5,08
PS1: R-785.0-1.0; CONV_R-785.0-1.0
P_1A, P_1B, P_1B1, P_1B2, P_1B3, P_1B4, P_1B5, P_2A, P_2B: SMD5; SMD2,54-5,08
P_A: SMD5; SMD2,54-5,08
P_B: SMD5; SMD2,54-5,08
P_C: SMD5; SMD2,54-5,08
P_CAM: SMD5; SMD2,54-5,08
P_D: SMD5; SMD2,54-5,08
P_GND: SMD5; SMD2,54-5,08
R1, R2, R3, R4, R5, R6, R7, R8, R9, R10, R11, R12, R13, R14, R15, R16, R17, R18, R19, R20, R21, R22, R23: R-EU_R0603; R0603
S_1A, S_1B, S_2A, S_2B: SMD5; SMD2,54-5,08
T1: BC847; SOT23
VMOT: SMD5; SMD2,54-5,08
WEMOS_RST_3V3: FE08-1; FE08
WEMOS_TX_5V: FE08-1; FE08

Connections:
5V: C3.1, MC_P_EN_DIR.5, MC_P_VMOT_GND.7, MC_S_EN_DIR.5, MC_S_VMOT_GND.7, PS1.3 (+VOUT), WEMOS_TX_5V.8
A0: C1.1, R2.1, R3.2, WEMOS_RST_3V3.2
CAM: O2.15 (QA), R1.1
CLK: ENC.5, I1.3 (E)
CLK/SCK: I1.2 (CLK), O1.11 (SCK), O2.11 (SCK), P_1B1.1, WEMOS_RST_3V3.5
DT: ENC.4, I1.4 (F)
GND: C1.2, C2.2, C3.2, C4.2, C5.2, C6.2, D1.A, ENC.1, G_CAM.1, I1.8 (GND), I1.15 (INH), LED2.4 (C), LED2.5 (C), LED2.6 (C), LED3.4 (C), LED3.5 (C), LED3.6 (C), LED4.4 (C), LED4.5 (C), LED4.6 (C), LED5.4 (C), LED5.5 (C), LED5.6 (C), MC_P_EN_DIR.1, MC_P_VMOT_GND.2, MC_P_VMOT_GND.8, MC_S_EN_DIR.1, MC_S_VMOT_GND.2, MC_S_VMOT_GND.8, O1.8 (GND), O1.13 (G), O2.8 (GND), O2.13 (G), PS1.2 (GND), P_1B3.1, P_GND.1, R3.1, T1.2 (E), WEMOS_RST_3V3.1, WEMOS_TX_5V.7
L1B: O2.1 (QB), R6.2
L1G: R5.2, R20.2
L2B: O2.2 (QC), R9.2
L2G: O2.4 (QE), R12.2
L3B: O2.3 (QD), R8.2, R21.2
L3G: O2.5 (QF), R11.2, R22.2
L4B: O2.6 (QG), R15.2
L4G: O2.7 (QH), R14.2, R23.2
unnamed: R1.2, T1.1 (B)
unnamed: D1.K (C), P_CAM.1, T1.3 (C)
unnamed: LED2.3 (A), R5.1
unnamed: LED2.1 (A), R6.1
unnamed: P_D.1, R4.2, R17.2
unnamed: LED3.3 (A), R8.1
unnamed: LED3.1 (A), R9.1
unnamed: P_A.1, R7.2, R16.2
unnamed: LED4.3 (A), R11.1
unnamed: LED4.1 (A), R12.1
unnamed: P_B.1, R10.2, R18.2
unnamed: LED5.3 (A), R14.1
unnamed: LED5.1 (A), R15.1
unnamed: P_C.1, R13.2, R19.2
unnamed: LED2.2 (A), R20.1
unnamed: I1.14 (D), R13.1
unnamed: I1.13 (C), R10.1
unnamed: I1.12 (B), R7.1
unnamed: I1.11 (A), R4.1
unnamed: LED3.2 (A), R21.1
unnamed: LED4.2 (A), R22.1
unnamed: LED5.2 (A), R23.1
OE_QH: O2.9 (QH*), P_1B4.1
P1A: MC_P_VMOT_GND.5, P_1A.1
P1B: MC_P_VMOT_GND.6, P_1B.1
P2A: MC_P_VMOT_GND.4, P_2A.1
P2B: MC_P_VMOT_GND.3, P_2B.1
P_DIR: MC_P_EN_DIR.8, WEMOS_TX_5V.5
P_MS1: MC_P_EN_DIR.2, O1.3 (QD)
P_MS2: MC_P_EN_DIR.3, O1.4 (QE)
P_MS3: MC_P_EN_DIR.4, O1.5 (QF)
P_SLEEP: MC_P_EN_DIR.6, O1.7 (QH)
P_STEP: MC_P_EN_DIR.7, WEMOS_TX_5V.6
QH: I1.9 (QH), WEMOS_RST_3V3.6
RCK: O1.12 (RCK), O2.12 (RCK), P_1B2.1, WEMOS_RST_3V3.4
RX: WEMOS_TX_5V.2
S1A: MC_S_VMOT_GND.5, S_1A.1
S1B: MC_S_VMOT_GND.6, S_1B.1
S2A: MC_S_VMOT_GND.4, S_2A.1
S2B: MC_S_VMOT_GND.3, S_2B.1
SER: O1.14 (SER), WEMOS_RST_3V3.3
SER2/QH*: O1.9 (QH*), O2.14 (SER)
SH: I1.1 (SH/!LD), WEMOS_RST_3V3.7
SW: ENC.3, I1.5 (G)
S_DIR: MC_S_EN_DIR.8, WEMOS_TX_5V.3
S_MS1: MC_S_EN_DIR.2, O1.15 (QA)
S_MS2: MC_S_EN_DIR.3, O1.1 (QB)
S_MS3: MC_S_EN_DIR.4, O1.2 (QC)
S_SLEEP: MC_S_EN_DIR.6, O1.6 (QG)
S_STEP: MC_S_EN_DIR.7, WEMOS_TX_5V.4
TX: WEMOS_TX_5V.1
VCC: C4.1, C5.1, C6.1, ENC.2, I1.16 (VCC), O1.10 (SCL), O1.16 (VCC), O2.10 (SCL), O2.16 (VCC), P3V3.1, P_1B5.1, R16.1, R17.1, R18.1, R19.1, WEMOS_RST_3V3.8
VMOT: C2.1, MC_P_VMOT_GND.1, MC_S_VMOT_GND.1, PS1.1 (+VIN), R2.2, VMOT.1

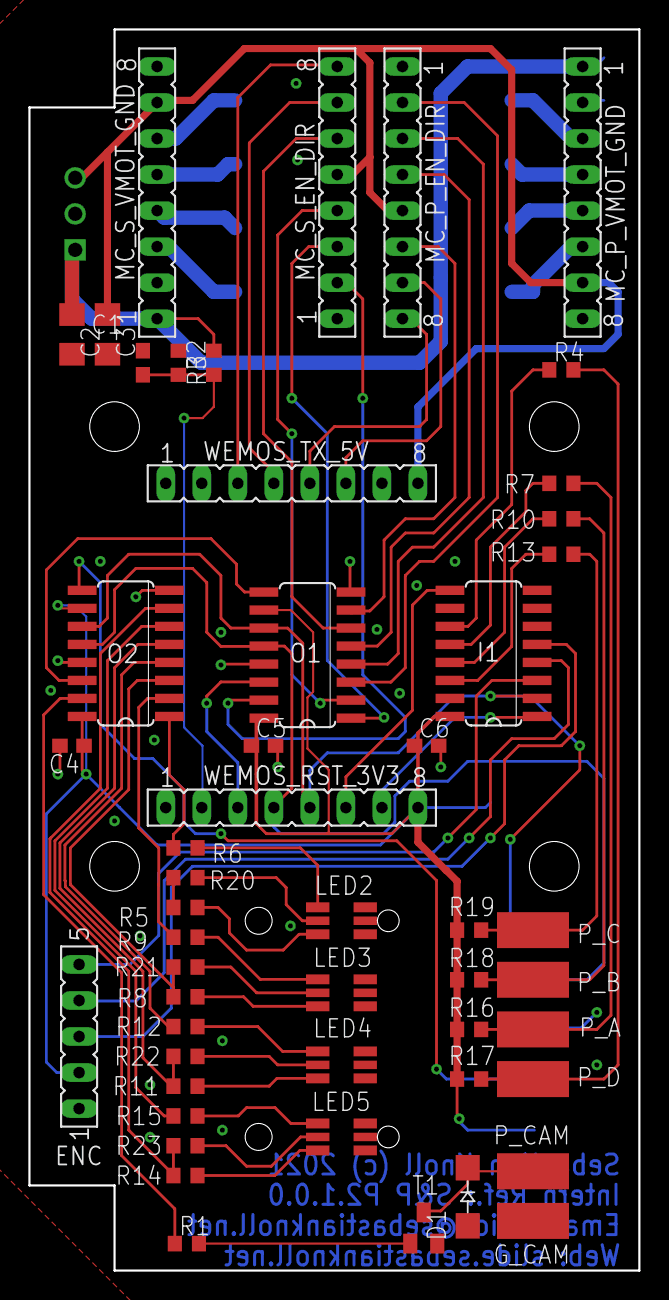
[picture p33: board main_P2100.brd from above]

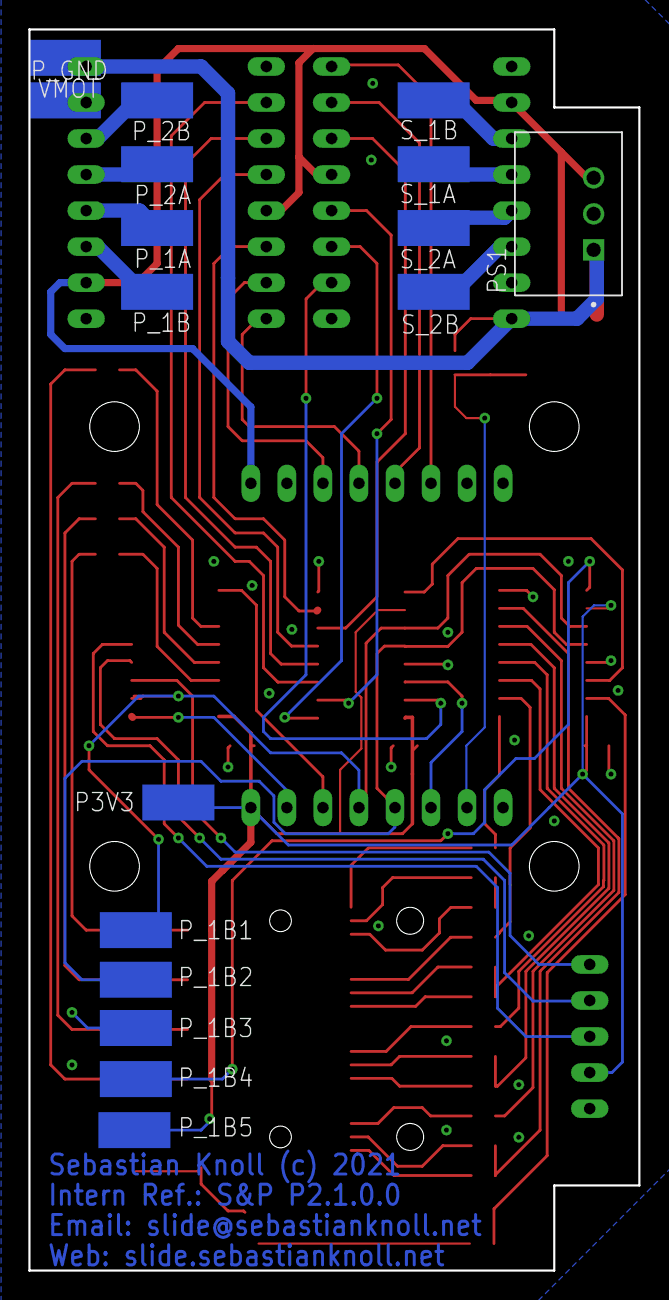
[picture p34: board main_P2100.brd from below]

Board: 2 copper layers, 43.0 x 87.5 mm, 68 parts (17 on the bottom side), 66 nets.

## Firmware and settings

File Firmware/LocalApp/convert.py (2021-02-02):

from os import listdir
from os.path import isfile, join


def getFiles():
    extensions = ["html", "js", "css"]
    return [f for f in listdir(".") if isfile(f) and 
            "." in  f and 
            "_min" not in f and
            f.split(".")[-1] in extensions]

TO_REPLACE = {  "%STATE%": "\" + getSliderStateString() + \"",
                "%STATE_DETAIL%": "\" + getSliderSubStateString() + \"",
                "%PAN%": "\" + String(getTimelapsePanSteps()) + \"",
                "%SLIDE%": "\" + String(getTimelapseSlideSteps()) + \"",
                "%PC%": "\" + String(getTimelapsePictureCount()) + \"",
                "%EXP%": "\" + String(getIOBoard()->getCameraExposureTime()) + \"",
                "%INT%": "\" + String(getTimelapseInterval()) + \"",
                "%SAP_NAME%": "\" + String(SLIDEANDPAN_NAME) + \"",
                "%SAP_VERSION%": "\" + String(SLIDEANDPAN_VERSION) + \"",
                "%SAP_VERSION_INFO%": "\" + String(SLIDEANDPAN_VERSION_INFO) + \"",
                "%SAP_CR%": "\" + String(SLIDEANDPAN_COPYRIGHT) + \"",
                "%SAP_ID%": "\" + String(SLIDEANDPAN_ID) + \"",
                "%SLIDEANDPAN_ID_INFO%": "\" + String(SLIDEANDPAN_ID_INFO) + \"",
                "%HANDBOOK%": "\" + String(SLIDEANDPAN_LINK_HANDBOOK) + \"",
                "%S_SLEEP%": "\" + String(getSlideStepper()->isSleeping() ? \"Sleeping\" : \"Awake\") + \"",
                "%S_NSLEEP%": "\" + String(getSlideStepper()->isSleeping() ? \"Awake\" : \"Sleep\") + \"",
                "%S_INSLEEP%": "\" + String(getSlideStepper()->isSleeping() ? 1 : 0) + \"",
                "%S_STEPS%": "\" + String(getSlideStepper()->getSteps()) + \"",
                "%S_TSTEPS%": "\" + String(getSlideStepper()->getTargetSteps()) + \"",
                "%S_SPEED%": "\" + String(getSlideStepper()->getSpeed()) + \"",
                "%S_TSPEED%": "\" + String(getSlideStepper()->getTargetSpeed()) + \"",
                "%S_RES%": "\" + String(getSlideStepper()->getResolution()) + \"",
                "%S_LAZY%": "\" + String(getSlideStepper()->isInLazyMode() ? \"Yes\" : \"No\") + \"",
                "%S_NLAZY%": "\" + String(getSlideStepper()->isInLazyMode() ? \"Go Strong\" : \"Go Lazy\") + \"",
                "%S_INLAZY%": "\" + String(getSlideStepper()->isInLazyMode() ? 0 : 1) + \"",
                "%S_PHY_VALUE_DES%": "\" + (getSlideStepper()->getPhysicalValueDescription()) + \"",
                "%S_PHY_VALUE%": "\" + (getSlideStepper()->getPhysicalValueInfo()) + \"",
                "%S_PHY_VALUE_UNIT%": "\" + (getSlideStepper()->getPhysicalValueUnit()) + \"",
                "%S_DIR_PIN%": "\" + String(SLIDE_STEPPER_PIN_DIRECTION) + \"",
                "%S_STEP_PIN%": "\" + String(SLIDE_STEPPER_PIN_STEP) + \"",
                "%S_SLEEP_PIN%": "\" + String(SLIDE_STEPPER_PIN_SLEEP) + \"",
                "%S_STEPS_PER_TURN%": "\" + String(STEPPER_STEPS_PER_TURN) + \"",
                "%S_CAN_CHANGE_RES%": "\" + String(getSlideStepper()->hasChangeResolutionMethod() ? \"Yes\" : \"No\") + \"",
                "%S_DRIVER_M1%": "\" + String(SLIDE_STEPPER_DRIVER_M1) + \"",
                "%S_DRIVER_M2%": "\" + String(SLIDE_STEPPER_DRIVER_M2) + \"",
                "%S_DRIVER_M3%": "\" + String(SLIDE_STEPPER_DRIVER_M3) + \"",
                "%P_SLEEP%": "\" + String(getPanStepper()->isSleeping() ? \"Sleeping\" : \"Awake\") + \"",
                "%P_NSLEEP%": "\" + String(getPanStepper()->isSleeping() ? \"Awake\" : \"Sleep\") + \"",
                "%P_INSLEEP%": "\" + String(getPanStepper()->isSleeping() ? 1 : 0) + \"",
                "%P_STEPS%": "\" + String(getPanStepper()->getSteps()) + \"",
                "%P_TSTEPS%": "\" + String(getPanStepper()->getTargetSteps()) + \"",
                "%P_SPEED%": "\" + String(getPanStepper()->getSpeed()) + \"",
                "%P_TSPEED%": "\" + String(getPanStepper()->getTargetSpeed()) + \"",
                "%P_RES%": "\" + String(getPanStepper()->getResolution()) + \"",
                "%P_LAZY%": "\" + String(getPanStepper()->isInLazyMode() ? \"Yes\" : \"No\") + \"",
                "%P_NLAZY%": "\" + String(getPanStepper()->isInLazyMode() ? \"Go Strong\" : \"Go Lazy\") + \"",
                "%P_INLAZY%": "\" + String(getPanStepper()->isInLazyMode() ? 0 : 1) + \"",
                "%P_PHY_VALUE_DES%": "\" + (getPanStepper()->getPhysicalValueDescription()) + \"",
                "%P_PHY_VALUE%": "\" + (getPanStepper()->getPhysicalValueInfo()) + \"",
                "%P_PHY_VALUE_UNIT%": "\" + (getPanStepper()->getPhysicalValueUnit()) + \"",
                "%P_DIR_PIN%": "\" + String(PAN_STEPPER_PIN_DIRECTION) + \"",
                "%P_STEP_PIN%": "\" + String(PAN_STEPPER_PIN_STEP) + \"",
                "%P_SLEEP_PIN%": "\" + String(PAN_STEPPER_PIN_SLEEP) + \"",
                "%P_STEPS_PER_TURN%": "\" + String(STEPPER_STEPS_PER_TURN) + \"",
                "%P_CAN_CHANGE_RES%": "\" + String(getPanStepper()->hasChangeResolutionMethod() ? \"Yes\" : \"No\") + \"",
                "%P_DRIVER_M1%": "\" + String(PAN_STEPPER_DRIVER_M1) + \"",
                "%P_DRIVER_M2%": "\" + String(PAN_STEPPER_DRIVER_M2) + \"",
                "%P_DRIVER_M3%": "\" + String(PAN_STEPPER_DRIVER_M3) + \"",  
                "%SLIDE_GEAR_DIAMETER%": "\" + String(SLIDE_GEAR_DIAMETER) + \"",
                "%PAN_GEAR_SMALL_COG_NUMBER%": "\" + String(PAN_GEAR_SMALL_COG_NUMBER) + \"",
                "%PAN_GEAR_LARGE_COG_NUMBER%": "\" + String(PAN_GEAR_LARGE_COG_NUMBER) + \"",
                "%PIN_LATCH%": "\" + String(PIN_LATCH) + \"",
                "%PIN_CLOCK%": "\" + String(PIN_CLOCK) + \"",
                "%PIN_DATAOUT%": "\" + String(PIN_DATAOUT) + \"",
                "%PIN_DATAIN%": "\" + String(PIN_DATAIN) + \"",
                "%PIN_LATCHIN%": "\" + String(PIN_LATCHIN) + \"",
                "%ENCODER_PIN_CLK%": "\" + String(ENCODER_PIN_CLK) + \"",
                "%ENCODER_PIN_DIRECTION%": "\" + String(ENCODER_PIN_DIRECTION) + \"",
                "%ENCODER_PIN_SWITCH%": "\" + String(ENCODER_PIN_SWITCH) + \"",
                "%PIN_BATTERY%": "\" + String(PIN_BATTERY) + \"",
                "%EARTH_TIME_PER_DAY%": "\" + secondsToString(EARTH_SECONDS_PER_DAY) + \"",
                "%MOON_TIME_PER_TURN%": "\" + secondsToString(MOON_SECONDS_PER_TURN) + \"",
                "%TIMELAPSE_TOTAL_TIME%": "\" + secondsToString(getTimelapseTotalTime()) + \"",
                "%TIMELAPSE_END_TIME%": "\" + secondsToTimeString(getTimelapseEndTime()) + \"",
                "%TIMELAPSE_VIDEO_LENGTH_24FPS%": "\" + secondsToString(getTimelapseVideoTimePrediction(24)) + \"",
                "%TIMELAPSE_VIDEO_LENGTH_25FPS%": "\" + secondsToString(getTimelapseVideoTimePrediction(25)) + \"",
                "%TIMELAPSE_VIDEO_LENGTH_30FPS%": "\" + secondsToString(getTimelapseVideoTimePrediction(30)) + \"",
                "%TIMELAPSE_VIDEO_LENGTH_60FPS%": "\" + secondsToString(getTimelapseVideoTimePrediction(60)) + \"",
                "%TIMELAPSE_TOTAL_SLIDE%": "\" + String(getTimelapseTotalSlideDistance()) + \"",
                "%TIMELAPSE_TOTAL_PAN%": "\" + String(getTimelapseTotalPanDistance()) + \"",
                "%TIME%": "\" + secondsToTimeString(getTime()) + \"",
                "%DARK_MODE_NV%": "\" + String(isSliderInDarkMode() ? 0 : 1) + \"", 
                "%DARK_MODE%": "\" + String(isSliderInDarkMode() ? \"is On\" : \"is Off\") + \"",
                "%LOGS%": "\" + getRingBufferForWeb() + \"",
                "%BATTERY_LVL%": "\" + String(getIOBoard()->getBatteryLevel()) + \"",
                "%TIMELAPSE_HEMISPHERE%": "\" + String(isTimelapseInNortherHemisphere() ? \"Northern\" : \"South\") + \"",
                "%TIMELAPSE_HEMISPHERE_NV%": "\" + String(!isTimelapseInNortherHemisphere() ? 1 : 0) + \""
            }

fileContent = ""
def convert(file):
    global fileContent

    if not "." in file:
        print("Convert {} failed (Ext not found) ".center(80, "-"))
        return 

    print(" Convert {} ".format(file).center(80, "-"))
    content = open(file, "r").read()

    content = content.replace("'", "**R**").replace("\"", "'").replace("**R**", "\\\"")
    content = content.replace("\t", " ").replace("\n", "\"));\n\tserver.sendContent(F(\"").replace("  ", " ")
    for tore in TO_REPLACE: 
        content = content.replace(tore, TO_REPLACE[tore].replace("\" +", "\"));\n\tserver.sendContent(").replace("+ \"", ");\n\tserver.sendContent(F(\""))

    filename = file.split(".")[0:-1]
    fileContent += "\n\nvoid " + filename[0].capitalize() + "AppPageHandler(ESP8266WebServer& server) {\n"
    fileContent += "\tserver.sendContent(F(\"" + content
    fileContent = fileContent.replace("\"\"", "\"\\n\"")
    fileContent += "\"));\n}"

def initFileContent():
    global fileContent

    fileContent = """
#ifndef HTML_APPFILES_H
#define HTML_APPFILES_H

#include "common.h"
#include "io.h"
#include "stepper.h"
#include "debug.h"
    """

def writeFile():
    global fileContent

    fileContent += "\n\n#endif"
    
    newFile = open("htmlAppFiles.h", "w+")
    newFile.write(fileContent)
    newFile.close()

def main():
    initFileContent()

    files = getFiles()

    print(" Files: ".center(80, "-"))
    print(files)

    for file in files: convert(file)

    writeFile()


if __name__ == "__main__":
    main()

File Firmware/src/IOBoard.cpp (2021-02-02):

#include "IOBoard.h"

String byteToBinaryString(uint8_t word) {
    String result = "";

    for(uint8_t index = 128; index > 0; index/=2) result += (word & index) ? "1" : "0";

    return result;
}

IOBoard::IOBoard(   pin_t setLatchPin,
                    pin_t setClockPin,
                    pin_t setDataOutPin,
                    ioport_t numOutputs,
                    pin_t setLatchInPin,
                    pin_t setDataInPin,
                    ioport_t numInputs) {

    outputState = 0;

    latchPin = setLatchPin;
    clockPin = setClockPin;
    dataOutPin = setDataOutPin;

    dataInPin = setDataInPin;
    latchInPin = setLatchInPin;

    numberOutputPorts = numOutputs;
    numberInputPorts = numInputs;

    cameraExposureTime = CAM_TIME_EXPOSURE_DEFAULT;
    cameraStatus = CAM_STATE_IDLE;

    setup();

    applyOutputState();

    commonTicker.attach_ms(100, [this](){ this->commonTick(); } );

    updateBatteryLevel();
}

void IOBoard::blinkTick() {
    blinkHalfSecond = (blinkHalfSecond == HIGH) ? LOW : HIGH;
    
    if(blinkHalfSecond == HIGH) {
        blinkSecond = (blinkSecond == HIGH) ? LOW : HIGH;
    }
}

void IOBoard::commonTick() {
    commonTickerCounter++;

    if(commonTickerCounter % 5 == 0) {
        blinkTick();
    }

    if(commonTickerCounter >= 20) {
        commonTickerCounter = 0;
        batteryTick();
    }
    
    cameraTick();

    incTimeByMinimumStep();

    timeCounter++;
    if(timeCounter >= ((clock_t)-1)) timeCounter = 0;
}

void IOBoard::cameraTick() {
    cameraIntervalCounter+=TIME_RESOLUTION;

    switch (cameraGetStatus())
    {
        case CAM_STATE_IDLE:
            cameraIntervalCounter = 0;
        break;

        case CAM_STATE_PREPARE:
            if(cameraIntervalCounter >= CAM_TIME_PREPARE) {
                cameraStatus = CAM_STATE_PHOTO;
                debugMessage("CamStatus: Photo (" + secondsToTimeString(getTime()) + ")");
                cameraIntervalCounter = 0;
            }
        break;

        case CAM_STATE_PHOTO:
            if(cameraIntervalCounter >= cameraExposureTime) {
                cameraStatus = CAM_STATE_REST;
                debugMessage("CamStatus: Rest (" + secondsToTimeString(getTime()) + ")");
                cameraIntervalCounter = 0;
            }
        break;

        case CAM_STATE_REST:
            if(cameraIntervalCounter >= CAM_TIME_REST) {
                cameraStatus = CAM_STATE_IDLE;
                debugMessage("CamStatus: Idle (" + secondsToTimeString(getTime()) + ")");
                cameraIntervalCounter = 0;
            }
        break;

        default:
            debugMessage("CamStatus: Default (" + secondsToTimeString(getTime()) + ")");
        break;
    }
}

void IOBoard::batteryTick() {
    updateBatteryLevel();
}

void IOBoard::setup() {

    pinMode(latchPin, OUTPUT);
    pinMode(clockPin, OUTPUT);
    pinMode(dataOutPin, OUTPUT);

    pinMode(dataInPin, INPUT);
    pinMode(latchInPin, OUTPUT);
}

String IOBoard::getBatteryStream() {
    String stream = "\"battery\": {";
    stream += " \"level\": " + String(batteryLevel);
    stream += ", \"full\":" + String(BATTERY_GREEN_MIN);
    stream += ", \"middle\":" + String(BATTERY_ORANGE_MIN);
    stream += ", \"empty\":" + String(BATTERY_RED_MIN);
    stream += ", \"critical\":" + String(BATTERY_RED_BLINK_MIN);

    return stream + "}";
}


String IOBoard::cameraGetStatusString() {
    switch(cameraGetStatus()) {
        case CAM_STATE_IDLE: return "idle";
        case CAM_STATE_PHOTO: return "photo";
        case CAM_STATE_PREPARE: return "prepare";
        case CAM_STATE_REST: return "rest";
        default: return "?";
    }
}

void IOBoard::applyOutputState() {
    
    digitalWrite(latchPin, LOW);

    unsigned int boardNum = ceil(numberOutputPorts/8);

    for(unsigned int index = boardNum; index > 0; index--) {
        uint8_t value = ((outputState >> (8*(index-1))) & 0xFF);        
        shiftOut(dataOutPin, clockPin, MSBFIRST, value);
    }
    
    digitalWrite(latchPin, HIGH);
}

ioport_t oldLevel = HIGH;
void IOBoard::setOutput(ioport_t port, ioport_level_t level) {
    if(port >= numberOutputPorts) return;

    unsigned int mask = (1 << port);
    if(level == HIGH) outputState |= mask;
    else  outputState &= (~mask);
}

unsigned int IOBoard::getOutputState(ioport_t port) {
    return ((outputState & (1 << port)) == 0 ? LOW : HIGH);
}

void IOBoard::toggleOutput(ioport_t port) {
    setOutput(port, getOutputState(port) == LOW ? HIGH : LOW);
}
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

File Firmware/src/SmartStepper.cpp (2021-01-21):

#include "SmartStepper.h"
#include "io.h"

SmartStepper::SmartStepper(pin_t setDirectionPin, pin_t setStepPin, pin_t setSleepPin)
{
    debugMessage("SmartStepper: new Stepper (current #" + String(SmartStepper::steppers.size()) + ")");

    name = "<NOT SPECIFIED>";
    lazyMode = false;

    pinDirection = setDirectionPin;
    pinSleep = setSleepPin;
    pinStep = setStepPin;

    pinMode(pinDirection, OUTPUT);
    pinMode(pinStep, OUTPUT);
    //pinMode(pinSleep, OUTPUT);

    setResolution(MICROSTEPRESOLUTION::SIXTEENTH);
    setChangeResolutionMethod(nullptr);

    steps = 0;
    targetSteps = 0;

    speedMin = .05;
    setTargetSpeed(1);
    setSpeed(0);

    setTargetAcceleration(1);

    //ticker.attach_ms_scheduled(1, [this](){ this->tick(); });

    timerCount = 0;
    if(SmartStepper::steppers.size() <= 0) {
        SmartStepper::INIT_TIMER();
    }

    SmartStepper::steppers.push_back(this);
}

SmartStepper::~SmartStepper()
{
    std::vector<SmartStepper*>::iterator it = SmartStepper::steppers.begin();
    while(it != SmartStepper::steppers.end()) {
        if(*it == this) {
            it = SmartStepper::steppers.erase(it);
        }
        else
        {
            it++;    
        }
    }

    debugMessage("SmartStepper: removed Stepper (still #" + String(SmartStepper::steppers.size()) + ")");
}

std::vector<SmartStepper*> SmartStepper::steppers;
time_count_t SmartStepper::tickDeltaCount = 0;

void SmartStepper::INIT_TIMER(void) {

    debugMessage("SmartStepper: Init timer");

    noInterrupts();
    timer0_isr_init();
    timer0_attachInterrupt(SmartStepper::TICK);
    timer0_write(ESP.getCycleCount() + 80000000L); // 80MHz == 1sec
    interrupts();
}

void SmartStepper::TICK(void) {
    
    time_count_t start = ESP.getCycleCount();

    for(SmartStepper* stepper : SmartStepper::steppers) {
        stepper->internTick();
    }
    
    time_count_t delta = CPU_CLK_FREQ / SmartStepper::TICK_INTERRUPT_FREQ;

    SmartStepper::tickDeltaCount = ESP.getCycleCount() - start;

    timer0_write(ESP.getCycleCount()+delta); 
}

void SmartStepper::internTick() {
    timerCount++;
    
    setAcceleration();

    if(fabs(acceleration) > 0) {
        acceleration_t accelerationPerTick = acceleration / SmartStepper::TICK_INTERRUPT_FREQ;
        setSpeed(speed + accelerationPerTick);
    }

    if((timerCount) % speedModulo == 0) doStep();
    if(timerCount >= SmartStepper::TICK_INTERRUPT_FREQ) timerCount = 0;
}

void SmartStepper::setSpeedModulo() {
    float stepsPerSecond = speed * stepsPerTurn;
    float res = resolutionToSteps() * SmartStepper::TICK_INTERRUPT_FREQ;
    
    speedModulo = max((time_count_t)(round(res/stepsPerSecond)), (time_count_t)1);
}

steps_t SmartStepper::resolutionToSteps() {
    switch (resolution)
    {
        case MICROSTEPRESOLUTION::FULL: return 1;
        case MICROSTEPRESOLUTION::HALF: return .5;
        case MICROSTEPRESOLUTION::QUARTER: return .25;
        case MICROSTEPRESOLUTION::EIGHTH: return .125;
        case MICROSTEPRESOLUTION::SIXTEENTH: return .0625;
        default:
            debugError("Resolution not known!"); 
            return 0;
    }
}

void SmartStepper::setChangeResolutionMethod(std::function<void (MICROSTEPRESOLUTION)> setChangeResolutionMethod) {
    changeResolutionMethod = setChangeResolutionMethod;
}


void SmartStepper::setIdealResolutionIfPossible() {
    if(changeResolutionMethod) {
        MICROSTEPRESOLUTION resolution = calculateIdealResolutionFromSpeed();
        changeResolutionMethod(resolution);
        setResolution(resolution);
    }
}

MICROSTEPRESOLUTION SmartStepper::calculateIdealResolutionFromSpeed() {
    if(speed >= 2) return MICROSTEPRESOLUTION::FULL;
    else if(speed >= 1) return MICROSTEPRESOLUTION::HALF;
    else if(speed >= .5) return MICROSTEPRESOLUTION::QUARTER;
    else if(speed >= .25) return MICROSTEPRESOLUTION::EIGHTH;
    else if(speed >= .125) return MICROSTEPRESOLUTION::SIXTEENTH;

    return MICROSTEPRESOLUTION::SIXTEENTH;
}


void SmartStepper::setAcceleration() {
    acceleration = 0;

    speed_t curentTargetSpeed = targetSpeed;
    steps_t delta_steps = fabs(targetSteps - steps);
    if((speed * speed * stepsPerTurn / (2 * targetAcceleration)) >= delta_steps) curentTargetSpeed = 0;

    speed_t delta_speed = curentTargetSpeed - speed;
    if(fabs(delta_speed) < speedMin) {
        setSpeed(targetSpeed);
    }
    else {
        acceleration = (delta_speed > 0) ? targetAcceleration : (-1 * targetAcceleration);
    }

    /*if(timerCount % 5000 == 0)
        debugMessage("Speed: " + String(speed) + "\tTarget speed: " + String(targetSpeed) + "\tDelta steps: " + String(delta_steps) + "\tAcc: " + String(acceleration));
    */
}

void SmartStepper::doStep() {

    if(targetSteps == steps) {
        //if(isInLazyMode() && !isSleeping()) setSleepState(SLEEP);
        if(isInLazyMode()) setSleepState(SLEEP);
        return;
    }
    
    setDirection((targetSteps > steps) ? DIRECTION::FORWARD : DIRECTION::BACKWARD);

    setSleepState(AWAKE);

    digitalWrite(pinStep , LOW); 
    digitalWrite(pinStep , HIGH);

    steps_t made_steps = resolutionToSteps();
    steps += ((direction == DIRECTION::FORWARD) ? made_steps : -made_steps);

}

void SmartStepper::setTargetSteps(steps_t setTargetSteps) {
    steps_t resolution = resolutionToSteps();

    targetSteps = setTargetSteps - fmod(setTargetSteps, resolution);
}

void SmartStepper::setSleepState(SLEEPSTATE setState) {
    //digitalWrite(pinSleep, ((setState == SLEEPSTATE::SLEEP) ? LOW : HIGH));
    //IMP getIOBoard()->setAndApplyOutput(pinSleep, ((setState == SLEEPSTATE::SLEEP) ? LOW : HIGH));
    getIOBoard()->setOutput(pinSleep, ((setState == SLEEPSTATE::SLEEP) ? LOW : HIGH));
    sleepState = setState;
}

void SmartStepper::setSpeed(speed_t setSpeed) { 
    speed = min(max(setSpeed, speedMin), getMaxSpeed());
    setSpeedModulo();
}

void SmartStepper::setTargetSpeed(speed_t setTargetSpeed) {
    targetSpeed = min(max(setTargetSpeed, speedMin), getMaxSpeed());
}

void SmartStepper::setTargetAcceleration(acceleration_t setAcc) {
    acceleration_t minAcc = 0.01;
    acceleration_t maxAcc = 20;
    targetAcceleration = min(max(setAcc, minAcc), maxAcc);
}

speed_t SmartStepper::getMaxSpeed() {
    speed_t technical_possible = resolutionToSteps() * SmartStepper::TICK_INTERRUPT_FREQ / stepsPerTurn;
    return min(technical_possible, (speed_t)20);
}

void SmartStepper::setResolution(MICROSTEPRESOLUTION setRes) {
    resolution = setRes;
    if(changeResolutionMethod) changeResolutionMethod(setRes);

    setSpeed(speed);
}
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

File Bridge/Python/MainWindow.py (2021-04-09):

from PyQt5 import QtCore, QtGui, QtWidgets
from PyQt5.QtCore import QObject, QThread, pyqtSignal

from SerialFunctions import serialPortList
from Common import getFirmwareListEndpoint, getMockVersionJson, getFirmwareEndpoint

import os
import time
import urllib.request, json
import esptool
import subprocess

firmwareToProgramm = None
firmwareKey = None
serialPortToUse = None

class Ui_MainWindow(object):

    knownFirmwares = []

    def setupUi(self, MainWindow):
        MainWindow.setObjectName("MainWindow")
        MainWindow.resize(800, 600)
        sizePolicy = QtWidgets.QSizePolicy(QtWidgets.QSizePolicy.Fixed, QtWidgets.QSizePolicy.Fixed)
        sizePolicy.setHorizontalStretch(0)
        sizePolicy.setVerticalStretch(0)
        sizePolicy.setHeightForWidth(MainWindow.sizePolicy().hasHeightForWidth())
        MainWindow.setSizePolicy(sizePolicy)
        MainWindow.setMinimumSize(QtCore.QSize(800, 600))
        MainWindow.setMaximumSize(QtCore.QSize(800, 600))
        self.centralwidget = QtWidgets.QWidget(MainWindow)
        self.centralwidget.setObjectName("centralwidget")
        self.mdiArea_3 = QtWidgets.QMdiArea(self.centralwidget)
        self.mdiArea_3.setGeometry(QtCore.QRect(920, 0, 461, 551))
        brush = QtGui.QBrush(QtGui.QColor(177, 160, 160))
        brush.setStyle(QtCore.Qt.SolidPattern)
        self.mdiArea_3.setBackground(brush)
        self.mdiArea_3.setObjectName("mdiArea_3")
        self.label = QtWidgets.QLabel(self.centralwidget)
        self.label.setGeometry(QtCore.QRect(20, 190, 401, 21))
        font = QtGui.QFont()
        font.setFamily("MS Shell Dlg 2")
        font.setPointSize(14)
        self.label.setFont(font)
        self.label.setObjectName("label")
        self.comboBoxVersion = QtWidgets.QComboBox(self.centralwidget)
        self.comboBoxVersion.setGeometry(QtCore.QRect(20, 220, 751, 31))
        font = QtGui.QFont()
        font.setPointSize(14)
        self.comboBoxVersion.setFont(font)
        self.comboBoxVersion.setObjectName("comboBoxVersion")
        self.label_2 = QtWidgets.QLabel(self.centralwidget)
        self.label_2.setGeometry(QtCore.QRect(20, 360, 471, 21))
        font = QtGui.QFont()
        font.setFamily("MS Shell Dlg 2")
        font.setPointSize(14)
        self.label_2.setFont(font)
        self.label_2.setObjectName("label_2")
        self.comboBoxSerial = QtWidgets.QComboBox(self.centralwidget)
        self.comboBoxSerial.setGeometry(QtCore.QRect(20, 390, 751, 31))
        font = QtGui.QFont()
        font.setPointSize(14)
        self.comboBoxSerial.setFont(font)
        self.comboBoxSerial.setObjectName("comboBoxSerial")
        self.pushButtonStart = QtWidgets.QPushButton(self.centralwidget)
        self.pushButtonStart.setGeometry(QtCore.QRect(20, 500, 751, 61))
        font = QtGui.QFont()
        font.setPointSize(14)
        self.pushButtonStart.setFont(font)
        self.pushButtonStart.setObjectName("pushButtonStart")
        self.label_3 = QtWidgets.QLabel(self.centralwidget)
        self.label_3.setGeometry(QtCore.QRect(20, 430, 491, 21))
        font = QtGui.QFont()
        font.setFamily("MS Shell Dlg 2")
        font.setPointSize(14)
        self.label_3.setFont(font)
        self.label_3.setObjectName("label_3")
        self.label_4 = QtWidgets.QLabel(self.centralwidget)
        self.label_4.setGeometry(QtCore.QRect(20, 570, 151, 21))
        font = QtGui.QFont()
        font.setFamily("MS Shell Dlg 2")
        font.setPointSize(10)
        self.label_4.setFont(font)
        self.label_4.setObjectName("label_4")
        self.labelStatus = QtWidgets.QLabel(self.centralwidget)
        self.labelStatus.setGeometry(QtCore.QRect(70, 560, 1400, 41))
        font = QtGui.QFont()
        font.setFamily("BuRGfont TTF")
        font.setPointSize(8)
        self.labelStatus.setFont(font)
        self.labelStatus.setObjectName("labelStatus")
        self.label_5 = QtWidgets.QLabel(self.centralwidget)
        self.label_5.setGeometry(QtCore.QRect(40, 260, 41, 21))
        font = QtGui.QFont()
        font.setFamily("MS Shell Dlg 2")
        font.setPointSize(10)
        self.label_5.setFont(font)
        self.label_5.setObjectName("label_5")
        self.label_6 = QtWidgets.QLabel(self.centralwidget)
        self.label_6.setGeometry(QtCore.QRect(40, 280, 51, 21))
        font = QtGui.QFont()
        font.setFamily("MS Shell Dlg 2")
        font.setPointSize(10)
        self.label_6.setFont(font)
        self.label_6.setObjectName("label_6")
        self.label_7 = QtWidgets.QLabel(self.centralwidget)
        self.label_7.setGeometry(QtCore.QRect(40, 300, 81, 21))
        font = QtGui.QFont()
        font.setFamily("MS Shell Dlg 2")
        font.setPointSize(10)
        self.label_7.setFont(font)
        self.label_7.setObjectName("label_7")
        self.label_8 = QtWidgets.QLabel(self.centralwidget)
        self.label_8.setGeometry(QtCore.QRect(40, 320, 51, 21))
        font = QtGui.QFont()
        font.setFamily("MS Shell Dlg 2")
        font.setPointSize(10)
        self.label_8.setFont(font)
        self.label_8.setObjectName("label_8")
        self.labelFirmwareName = QtWidgets.QLabel(self.centralwidget)
        self.labelFirmwareName.setGeometry(QtCore.QRect(150, 250, 650, 41))
        font = QtGui.QFont()
        font.setFamily("BuRGfont TTF")
        font.setPointSize(8)
        self.labelFirmwareName.setFont(font)
        self.labelFirmwareName.setObjectName("labelFirmwareName")
        self.labelFirmwareVersion = QtWidgets.QLabel(self.centralwidget)
        self.labelFirmwareVersion.setGeometry(QtCore.QRect(150, 270, 650, 41))
        font = QtGui.QFont()
        font.setFamily("BuRGfont TTF")
        font.setPointSize(8)
        self.labelFirmwareVersion.setFont(font)
        self.labelFirmwareVersion.setObjectName("labelFirmwareVersion")
        self.labelFirmwareReleaseDate = QtWidgets.QLabel(self.centralwidget)
        self.labelFirmwareReleaseDate.setGeometry(QtCore.QRect(150, 290, 650, 41))
        font = QtGui.QFont()
        font.setFamily("BuRGfont TTF")
        font.setPointSize(8)
        self.labelFirmwareReleaseDate.setFont(font)
        self.labelFirmwareReleaseDate.setObjectName("labelFirmwareReleaseDate")
        self.labelFirmwareNotes = QtWidgets.QLabel(self.centralwidget)
        self.labelFirmwareNotes.setGeometry(QtCore.QRect(150, 310, 650, 41))
        font = QtGui.QFont()
        font.setFamily("BuRGfont TTF")
        font.setPointSize(8)
        self.labelFirmwareNotes.setFont(font)
        self.labelFirmwareNotes.setObjectName("labelFirmwareNotes")
        self.lineEditFirmwareKey = QtWidgets.QLineEdit(self.centralwidget)
        self.lineEditFirmwareKey.setEnabled(False)
        self.lineEditFirmwareKey.setGeometry(QtCore.QRect(530, 260, 241, 21))
        self.lineEditFirmwareKey.setPlaceholderText("")
        self.lineEditFirmwareKey.setObjectName("lineEditFirmwareKey")
        self.label_9 = QtWidgets.QLabel(self.centralwidget)
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

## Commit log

2020-03-29 Timer consts and waitUntilTargetReached
2020-04-12 Rotate with encoder
2021-01-16 Open Beta - Website crash fix and led fix
    [SmartStepper.cpp, common.h, io.cpp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]
2021-03-11 Electronic init commit
    [main.brd, main.sch, main_P2100.brd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]
2021-03-11 Organization init commit
    [PartList.xlsx]
2021-03-11 Construciton init commit
    [1590B2.igs, 1590B2.stp, 1590J.igs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]

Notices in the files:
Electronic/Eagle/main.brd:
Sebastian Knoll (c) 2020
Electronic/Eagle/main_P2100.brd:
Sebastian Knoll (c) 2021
